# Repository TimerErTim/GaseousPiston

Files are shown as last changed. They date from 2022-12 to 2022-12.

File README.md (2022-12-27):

# 3D-Printed LiquidPiston (GaseousPiston)

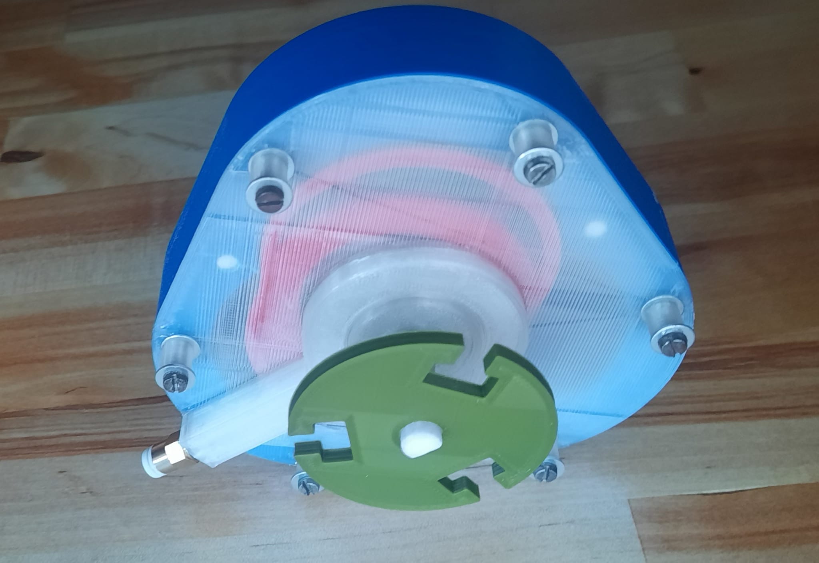
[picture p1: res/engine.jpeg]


---

This design uses a compressor with an air pressure of 8 bar. It is meant to be
3D-Printed and while it requires low tolerances, everything is parameterized, so you can edit it fitting for your
printer. It is also quite easy to assemble.

### Notes

- Even though model dimensions are unitless, it is designed to use mm. So a rotor with
  the radius of 10 is meant to be 20mm wide.

## Assembly

1. Print out all necessary parts - Model files with my configuration are in [`exported/`](exported).
    - Rotor
    - Housing
    - Cover
    - Crank shaft
    - Seal
    - (Depending on screw length: Cover nut)
2. Take something squishy (like a sponge) and put it into the apex seal holes of the housing
3. Put the crank shaft into the center of the rotor (you may use a ball bearing between the two parts - my config: MR128
   bearings)
4. Put the rotor inside the housing so that the gear of the rotor fits inside the involute gear of the housing
5. Place seals between the rotor and the apex seal holes filled with the squishy substance
6. Put the cover on the housing so that end of the crank shift fits through the center of the cover
7. Screw the cover on the housing (use the cover nut to account for extra long screws)
8. Screw the coupler into the air intake on the cover

## Usage

Attach a tube to the coupler and a compressor to the tube. Turn on the compressor and the engine begins to move. The
crank shaft begins to turn.

## Appendix

All of this works in theory and while the actual engine is buildable, it's not usable as of now. It is not
airtight enough and the rotor exhibits too much friction.

**Solution**: Even though the original idea was to only require one pneumatic intake coupler and to handle the air
distribution mechanically, one possible solution for this problem would be to individually provide each chamber with
air intake and to control each one of these with an electrical valve. Because the rotor then directly receives the
kinetic energy from the air flow, this approach should and - due to me testing this - would work. It may require more
air pressure though.

## Exporting from source

It is very likely that you want to tweak some numbers for your specific setup and tools.

The project uses [OpenSCAD](https://openscad.org/), therefore you need it too, in order to export the models.

The [`main.scad`](src/main.scad)
file under [`src`](src) includes all model parameters which are described in further detail down below. The
[`export.scad`](src/export.scad) file in the same folder can be used to export the individual parts, while
[`preview.scad`](src/preview.scad) can be used to preview the moving engine.

### Configuration

Parameter - Description pairs

- height - Rotor height
- bottom_thickness - Height/Thickness of the housing bottom
- center_hole_radius - Radius of the center hole in the rotor and cover
- crank_shaft_radius - Radius of the crank shaft
- crank_shaft_length - Usable length of the crank shaft sticking out of the cover
- d_shaft_length - Part length of the above length where the shaft becomes a D shaft
- counter_weight_distance - Distance between the counterweight and the housing
- counter_weight_width - The thickness of the counterweight
- rotor_radius - The overall size of the rotor and therefore whole engine
- rotor_center_wall_thickness - The wall thickness around the rotor's center hole
- rotor_inner_wall_thickness - The wall thickness inside the rotor (all walls except the other two kinds)
- rotor_outer_wall_thickness - The thickness of the wall separating chambers and the rotor insides
- seal_length - The length of the seals
- stator_outer_wall_thickness - The wall thickness for the housing (between chambers and outer world)
- stator_seal_depth - The depth of seal cutouts in the housing
- stator_seal_width - The width of the seals and their cutouts in the housing
- stator_seal_push_radius - The radius of the apex seal hole in the housing
- combustion_chamber_radius - The radius of the combustion chamber in the housing
- outlet_hole_radius - The radius of the holes on the bottom of the housing which serve as air outlets
- inlet_circle_radius - The radius of the air inlet on both the rotor and cover
- pneumatic_inlet_radius - The radius of the coupler/intake hole on the cover
- cover_thickness - The overall thickness of the cover (used for walls and center hole thickness)
- cover_height - The bottom area thickness of the cover
- cover_screw_radius - The radius of the screws used to attach the cover
- cover_screw_clearance - The extra radius given to the holes in the cover to provide a clear path for the screws
- cover_screw_length - The length of the screws used to attach the cover
- disk_thickness - The thickness of the disk attachable at the end of the crank shaft
- disk_radius - The radius of the disk attachable at the end of the crank shaft

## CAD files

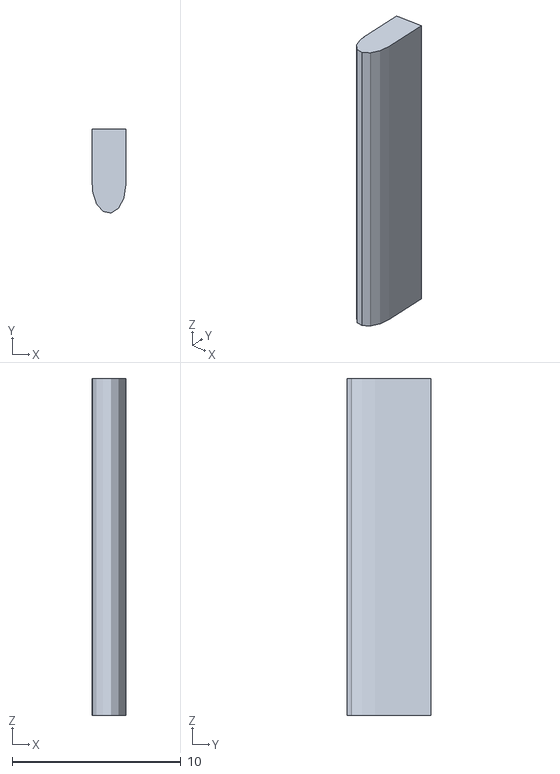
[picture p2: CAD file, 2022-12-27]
exported/seal.stl
2.00 x 4.99 x 20.0

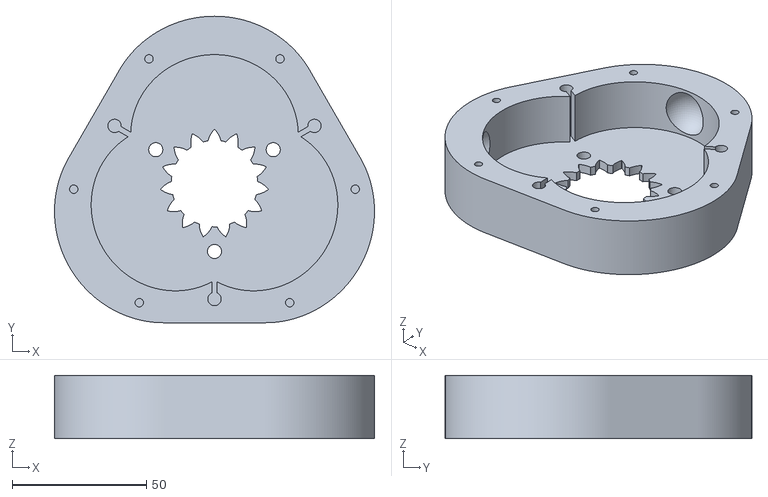
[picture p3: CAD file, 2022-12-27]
exported/housing.stl
119.1 x 114.1 x 23.5

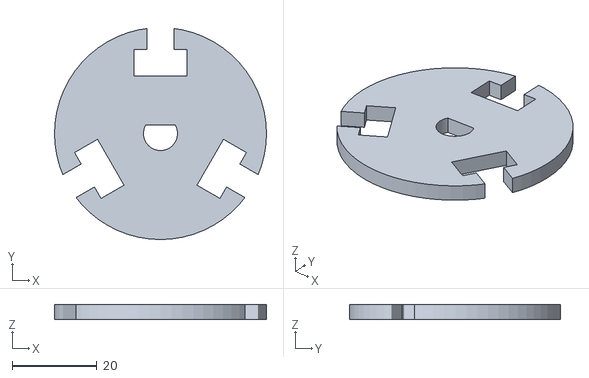
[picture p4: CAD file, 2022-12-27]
exported/disk.stl
50.0 x 49.8 x 3.50

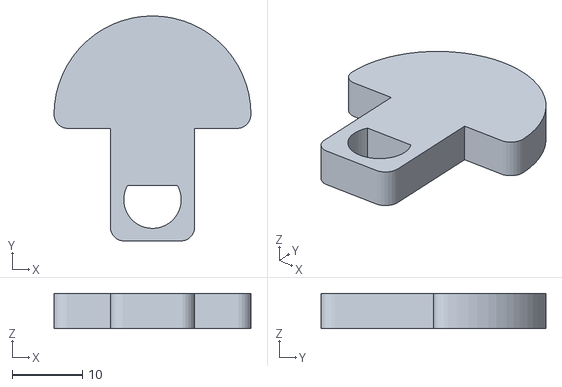
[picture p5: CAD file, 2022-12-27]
exported/counter_weight.stl
28.0 x 32.0 x 5.00

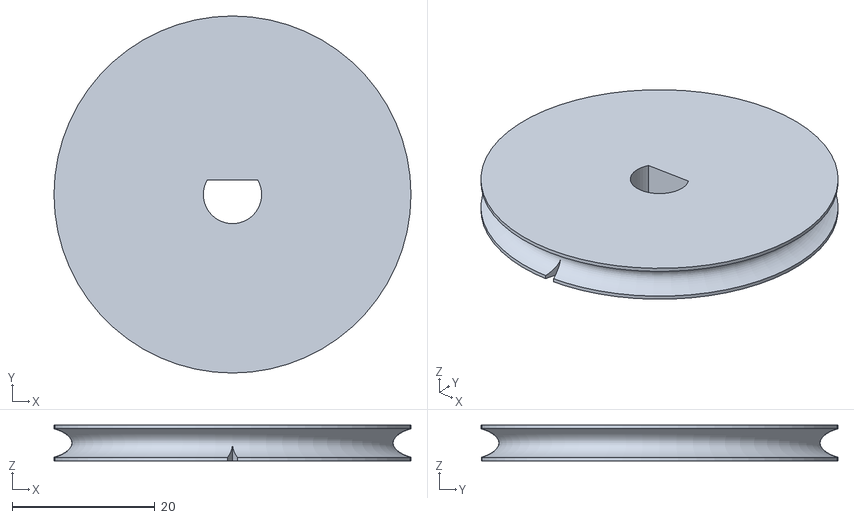
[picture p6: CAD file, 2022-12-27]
exported/guided_disk.stl
50.0 x 50.0 x 5.00

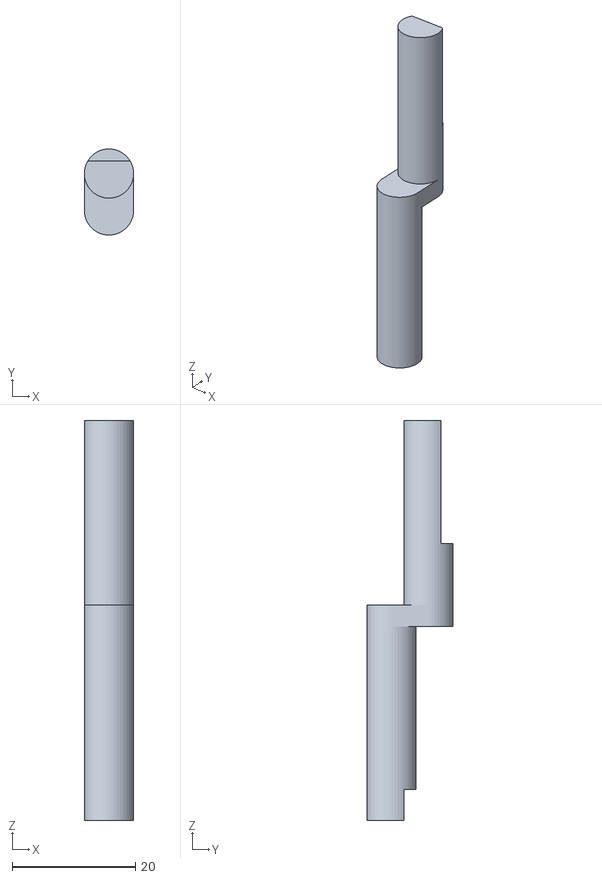
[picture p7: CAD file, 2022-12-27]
exported/crank_shaft.stl
7.99 x 14.0 x 65.0

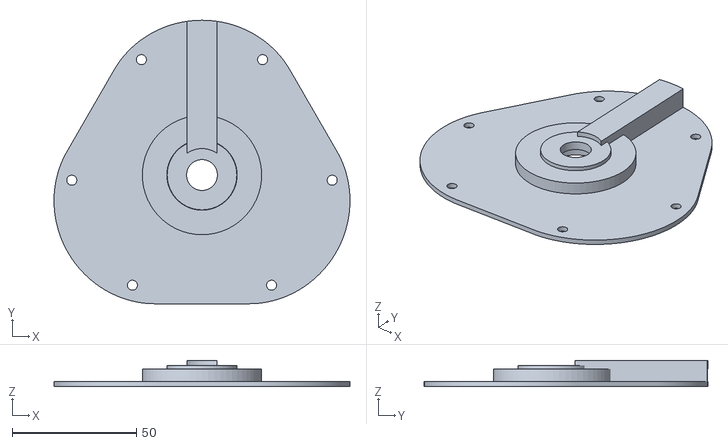
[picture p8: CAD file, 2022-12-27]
exported/cover.stl
119.1 x 114.1 x 10.5

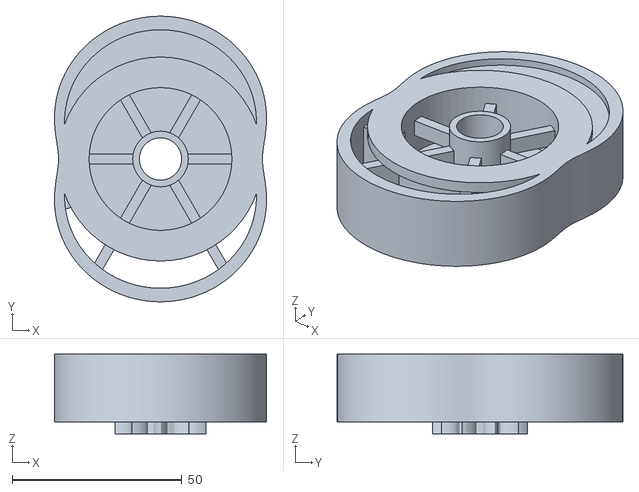
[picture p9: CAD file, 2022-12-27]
exported/rotor.stl
62.4 x 84.0 x 23.5

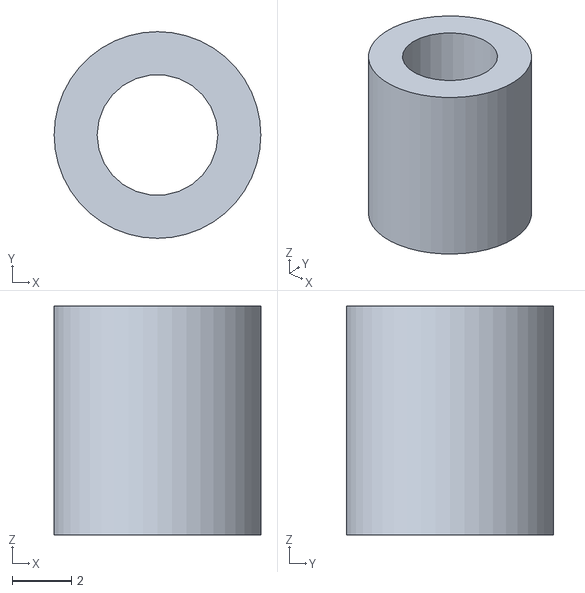
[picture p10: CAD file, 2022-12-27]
exported/cover_nut.stl
6.95 x 6.95 x 7.70

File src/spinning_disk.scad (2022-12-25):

include <main.scad>
use <crank_shaft.scad>
use <MCAD/regular_shapes.scad>

module disk_cutout() {
    translate([0, disk_radius, disk_thickness / 2])
        cube([disk_radius / 4, disk_radius / 2, disk_thickness + 0.002], center = true);

    translate([0, disk_radius / 1.5, disk_thickness / 2])
        cube([disk_radius / 2, disk_radius / 4, disk_thickness + 0.002], center = true);
}

module spinning_disk() {
    translate([0, 0, height + cover_thickness + crank_shaft_length - disk_thickness])
        difference() {
            cylinder(r = disk_radius, h = disk_thickness);

            circumscribed_r = (crank_shaft_radius) / cos(180 / max(round(4 * crank_shaft_radius), 3));
            translate([0, 0, - (height + cover_thickness + crank_shaft_length - disk_thickness) + 0.002])
                scale([circumscribed_r / crank_shaft_radius, circumscribed_r / crank_shaft_radius, 1]) crank_shaft();

            // Cutout some forms
            disk_cutout();
            rotate([0, 0, 120]) disk_cutout();
            rotate([0, 0, - 120]) disk_cutout();
        }
}

module guided_disk() {
    translate([0, 0, height + cover_thickness + crank_shaft_length - disk_thickness])
        difference() {
            cylinder(r = disk_radius, h = disk_thickness);

            circumscribed_r = (crank_shaft_radius) / cos(180 / max(round(4 * crank_shaft_radius), 3));
            translate([0, 0, - (height + cover_thickness + crank_shaft_length - disk_thickness) + 0.002])
                scale([circumscribed_r / crank_shaft_radius, circumscribed_r / crank_shaft_radius, 1]) crank_shaft();

            // Cutout guidelines
            translate([0, 0, disk_thickness / 2])
                oval_torus(disk_radius - 2.5, thickness = [2.5 * 5, disk_thickness]);

            // Cutout entering hook
            translate([0, - disk_radius, 0]) scale([1, 2, 1]) triangle_prism(disk_thickness / 2, 2.5 / 2);
        }
}

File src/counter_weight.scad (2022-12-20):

include <main.scad>
use <crank_shaft.scad>

module base_connector_shape() {
    minkowski() {
        translate([0, rotor_radius / 7 - crank_shaft_radius / 2])
            cube([crank_shaft_radius * 2, rotor_radius * 2 / 7 + crank_shaft_radius, counter_weight_width], center =
            true);

        cylinder(r = 2, h = 0.001);
    }
}

module basic_connector() {
    circumscribed_r = (crank_shaft_radius) / cos(180 / max(round(4 * crank_shaft_radius), 3));

    difference() {
        base_connector_shape();

        translate([0, rotor_radius / 7, bottom_thickness + (counter_weight_distance + counter_weight_width / 2) * 1.15])
            scale([circumscribed_r / crank_shaft_radius, circumscribed_r / crank_shaft_radius, 1.1]) crank_shaft();
    }
}

module weight() {
    translate([0, rotor_radius * 2 / 7, 0]) minkowski() {
        difference() {
            cylinder(r = rotor_radius * 2 / 7, h = counter_weight_width, center = true);

            translate([0, - rotor_radius / 7, 0])
                cube([rotor_radius * 4 / 7, rotor_radius * 2 / 7, counter_weight_width + 0.002], center = true);
        }

        cylinder(r = 2, h = 0.001);
    }
}

module counter_weight() {
    translate([0, - rotor_radius / 7, - bottom_thickness - counter_weight_distance - counter_weight_width / 2]) union()
        {
            basic_connector();
            weight();
        }
}

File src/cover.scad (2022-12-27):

include <main.scad>
use <housing.scad>
use <util.scad>
use <MCAD/regular_shapes.scad>

cutout_radius = rotor_radius / 7 + crank_shaft_radius + 0.5;

inlet_radius = min(inlet_circle_radius + rotor_radius / 7, rotor_radius * 4 / 7);
inlet_width = inlet_radius - max(center_hole_radius + rotor_center_wall_thickness + rotor_radius / 7,
max(cutout_radius + cover_thickness, center_hole_radius + cover_thickness));

inlet_length = rotor_radius * 8 / 7 + stator_outer_wall_thickness - inlet_radius;

module pneumatic_inlet() {
    intersection() {
        translate([- pneumatic_inlet_radius - cover_thickness, 0, cover_height])
            cube([pneumatic_inlet_radius * 2 + cover_thickness * 2, inlet_length * 2, pneumatic_inlet_radius * 2 +
                cover_thickness]);

        difference() {
            housing_base(height * 2);

            cylinder(r = inlet_radius - inlet_width - cover_thickness, h = height * 2);
        }
    }
}

module pneumatic_inlet_cutout() {
    translate([0, 0, cover_height - 0.002]) union() {
        intersection() {
            translate([- pneumatic_inlet_radius, 0, 0]) cube([pneumatic_inlet_radius * 2, inlet_length,
                    pneumatic_inlet_radius * 2]);

            cylinder_tube(height = pneumatic_inlet_radius * 2, radius = inlet_radius - cover_thickness, wall =
                inlet_width - cover_thickness);
        }

        translate([0, .002, 0]) intersection() {
            translate([0, 0, (pneumatic_inlet_radius)])
                rotate([- 90, 0, 0]) cylinder(r = pneumatic_inlet_radius, h = inlet_length * 2);

            difference() {
                housing_base(height * 2);

                cylinder(r = inlet_radius - inlet_width, h = height * 2);
            }
        }
    }
}

module cover() {
    translate([0, 0, height])
        difference() {
            union() {
                difference() {
                    housing_base(cover_height);

                    // Cutout screws
                    translate([0, 0, - height / 2 - 0.002]) clone([1, 0, 0]) {
                        cover_screw_cutout(cover_screw_radius + cover_screw_clearance);
                        rotate([0, 0, 120]) cover_screw_cutout(cover_screw_radius + cover_screw_clearance);
                        rotate([0, 0, - 120]) cover_screw_cutout(cover_screw_radius + cover_screw_clearance);
                    }
                }

                translate([0, 0, cover_height])
                    cylinder(r = max(cutout_radius + cover_thickness, center_hole_radius + cover_thickness), h =
                                cover_thickness * 2 + 1.5 - cover_height);

                // Add inlet ring
                translate([0, 0, cover_height - 0.001])
                    cylinder_tube(height = cover_thickness * 2 - cover_height, radius = inlet_radius, wall = inlet_width
                    );

                // Add pneumatic inlet
                pneumatic_inlet();
            }

            // Cutout inlet ring
            translate([0, 0, - .001])
                cylinder_tube(height = cover_thickness, radius = inlet_radius - cover_thickness, wall = inlet_width -
                    cover_thickness);

            // Cutout pneumatic inlet
            pneumatic_inlet_cutout();

            // Cutout crank shaft
            translate([0, 0, - .001]) polyhole(r = cutout_radius, h = cover_thickness + 1.5 + 0.002);

            // Cutout center hole
            translate([0, 0, cover_thickness + 1.5]) polyhole(r = center_hole_radius, h = cover_thickness + 0.002);
        }
}

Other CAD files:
src/parts/spinning_disk.scad
src/crank_shaft.scad
src/export.scad
src/housing.scad
src/main.scad
src/nut.scad
src/parts/counter_weight.scad
src/parts/cover.scad
src/parts/crank_shaft.scad
src/parts/housing.scad
src/parts/nut.scad
src/parts/rotor.scad
src/parts/seal.scad
src/preview.scad
src/rotor.scad
src/seal.scad
src/util.scad

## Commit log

2022-12-18 Abstract liquid piston size
    [rotor.scad]
2022-12-19 Almost restore housing to prev version
    [Prototype.scad, housing.scad, main.scad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]
2022-12-19 Add many things and much stuff
    [counter_weight.scad, crank_shaft.scad, housing.scad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]
2022-12-20 Add counter weight
    [counter_weight.scad, cover.scad, housing.scad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]
2022-12-21 Add none functioning cover
    [cover.scad, housing.scad, main.scad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]
2022-12-21 Finish cover
    [cover.scad, main.scad, preview.scad]
2022-12-25 Finish all stuff
    [cover.scad, housing.scad, main.scad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]
2022-12-27 Add cover height parameter
    [cover.scad, main.scad]
2022-12-27 Redo project structure
    [Prototype.scad, counter_weight.stl, cover.stl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]
2022-12-27 Add export file
    [counter_weight.scad, cover.scad, crank_shaft.scad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]
